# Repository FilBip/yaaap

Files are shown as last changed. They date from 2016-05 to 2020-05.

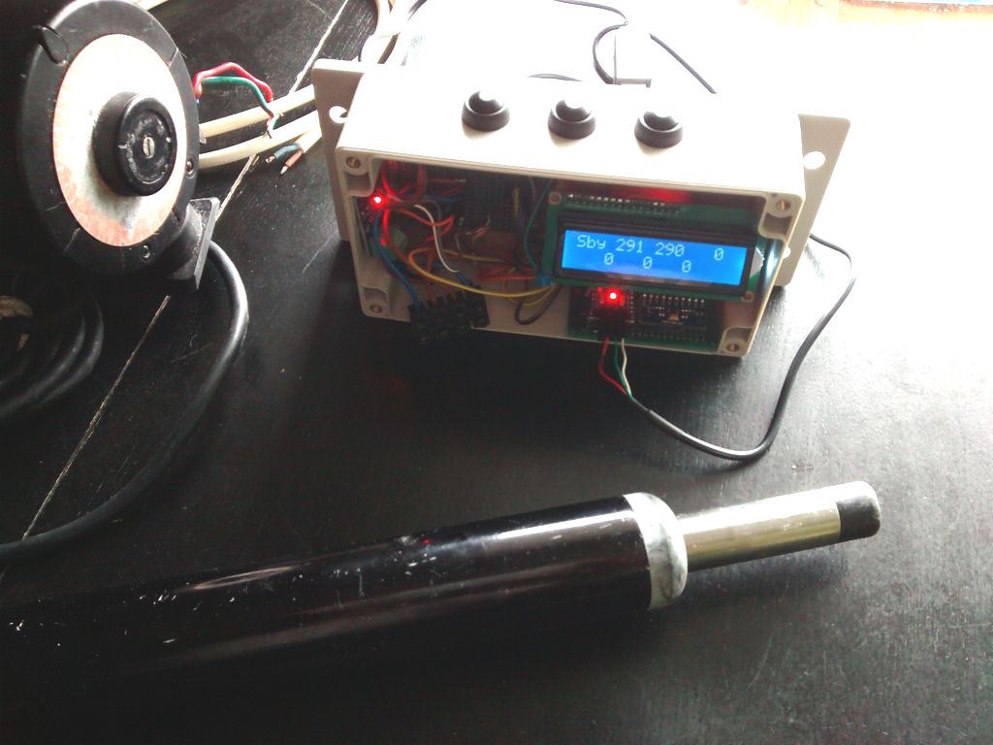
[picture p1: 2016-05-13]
yaaap-wip2.jpg

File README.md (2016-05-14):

# YAAAP Yet Another Arduino AutoPilot

Yaaap  is a simple autopilot for a sailboat using Arduino pro mini card and breakouts
The interface is reduced to 3 buttons and an LCD display.
The project was intended to replace the CPU of an old analog pilot Autohelm 2000 retaining the original electric actuator.

## Features

Heading is given by the 9dof IMU MPU9250 using the RTIMUlib for Arduino by Richards-Tech.
RTIMUlib filter is especially effective to keep a steady course when the heel angle varies.
I reduced the impact of magnetometer instability with a reduced SLERP value: fusion.setSlerpPower(0.001)
The tiller actuator is the old cylinder from the original Autohelm 2000 tillerPilot (with Omron motor 2332 12V)
Typical current for this motor is 1.6A. The cheap TB6612FNG can drive this motor with the 2 channels in parrallel (typical 2A to peak 6A).
It can be replaced by a more powerfull driver like IBT_2 with BTN7970B. 
I dropped the usage of PWM with my old small motor. Minimal pulse is 10ms, increasing to continuous depending on the computed command(PID).
There is no device to read the tiller position. Current to the motor is controlled to detect end of course or overload (ACS712).
The interface is minimal, made of 3 buttons using OneButtons library https://github.com/mathertel/OneButton
The LCD display is an I2C version.
   
## Instructions
The device is fixed behind the tiller facing the route.
Button 1 on the left: sarboard/less fonctions
button 2 on center: select/run-standby fonctions
Button 3 on the right: port/plus fonctions
	
### Startup
On startup, after initialization, the device is on standby, bearing to the current direction.
The display shows the status(Sby/Run), baering, heading and error (difference to baering).
   
### Run
click once on button 2.

### During run
click on button 1 or 3 increases (resp. decrease) 1 deg of bearing.
long press on button 1 or 3 increases (resp. decreases) 20 deg of bearing
long press on button 2 resets bearing to current heading
long press on button 1 and 2 (starboard and select) to tack to starboard
long press on button 3 and 2 (port and select) to tack to port
double click on button 2 to stop motor and standby
	
### During standby
long press button 1 push the tiller
long press button 3 pull the tiller
long press on button 2 resets bearing to current heading
long press button 1 and 3 to enter setup

### On setup first level
click 1(-) for dimmed backlight
click 3(+) for full backlight
click 2(sel) to enter setup menu
### On setup menu
click 1(-) to go to previous menu item
click 3(+) to go to next menu item
click 2(sel) to select menu item
### On setup item
click 1(-) to decrease value if applicable
click 3(+) to increase value if applicable
click 2(sel) to validate entry/value

### Calibration
To calibrate the compass, chose the menu item, draw 8 with the device. The display shows the offsets.
Click button 2 when OK.

### Configuration saving
Go to the saving menu item and validate to write calibration and other parameters to EEPROM

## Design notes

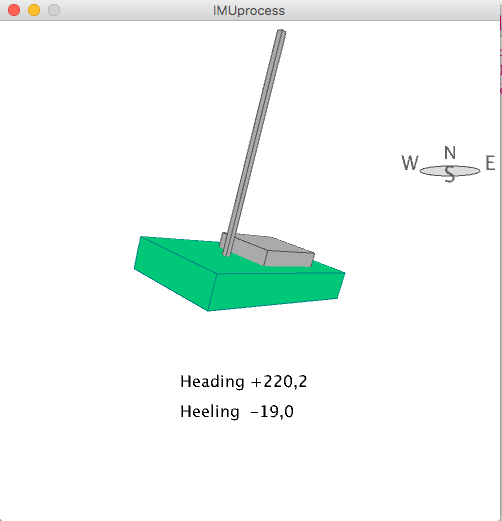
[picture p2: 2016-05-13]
YaaapProcessing/Processing snapshot.png

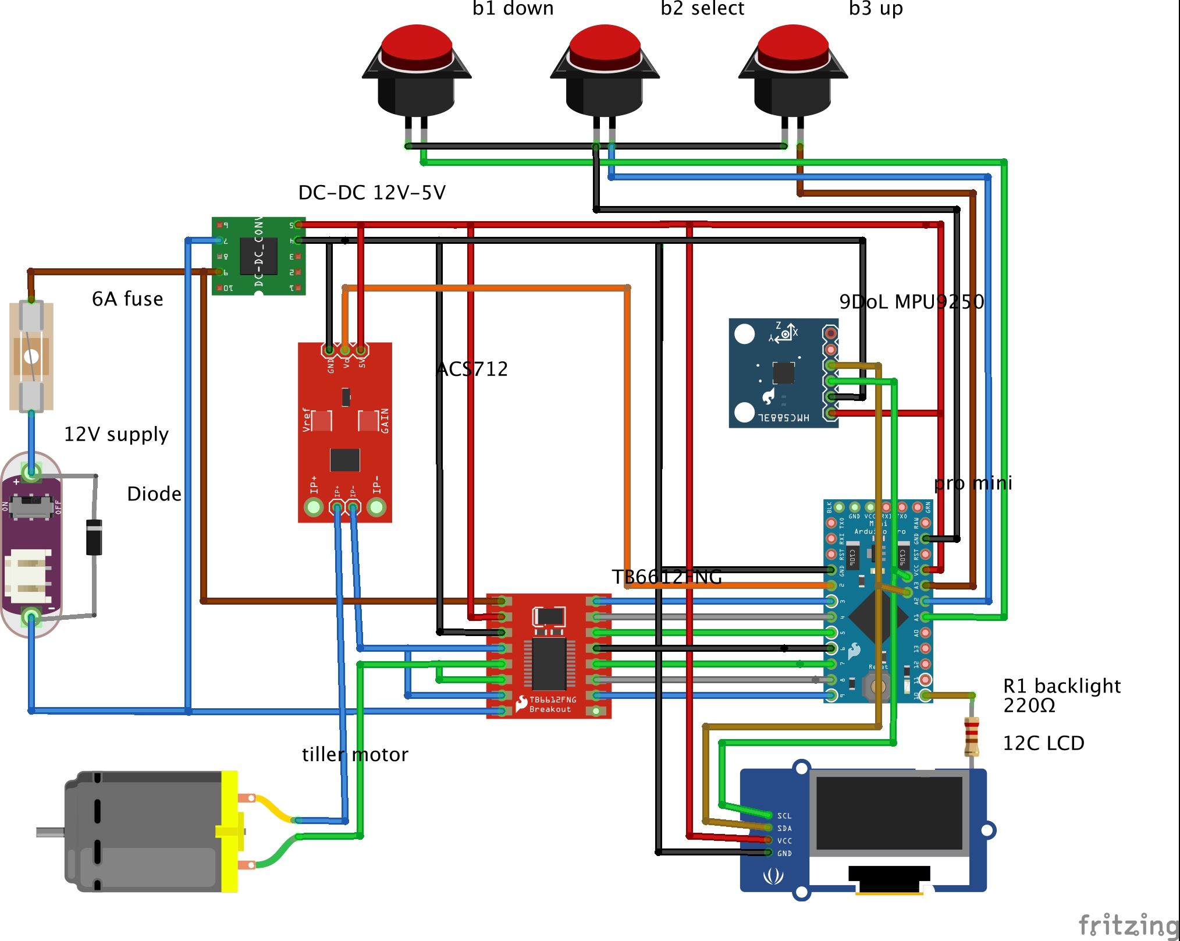
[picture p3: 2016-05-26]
fritz/yaaap_bb.jpg

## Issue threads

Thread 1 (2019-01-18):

yaaap.ino computeCmd function

odani, 2019-01-18:
Hi, can you confirm that line 363 in yaaap.ino is not necessary and that cmd should be computed on line 381 every time?

This is great code. I'm working on using it with a oled screen and a pololu lsm303 compass.

FilBip, 2019-01-18:
Hi,
on line 383, cmd should be computed... if not in deadband :)
A test "if (cmd != 0) cmd = ..." should be added on 383 or the bracket on 372 has to be moved after 383.

Code is not so great :))

regards

----- Mail original -----
De: "odani" <notifications@github.com>
À: "FilBip/yaaap" <yaaap@noreply.github.com>
Cc: "Subscribed" <subscribed@noreply.github.com>
Envoyé: Vendredi 18 Janvier 2019 02:21:40
Objet: [FilBip/yaaap] yaaap.ino computeCmd function (#1)

Hi, can you confirm that line 363 in yaaap.ino is not necessary and that cmd should be computed on line 381 every time?

This is great code. I'm working on using it with a oled screen and a pololu lsm303 compass.

—
You are receiving this because you are subscribed to this thread.
Reply to this email directly, view it on GitHub , or mute the thread .

FilBip, 2019-01-18:
My previous reply is wrong. The right solution is to move the bracket from 372 to 384.

----- Mail original -----
De: "odani" <notifications@github.com>
À: "FilBip/yaaap" <yaaap@noreply.github.com>
Cc: "Subscribed" <subscribed@noreply.github.com>
Envoyé: Vendredi 18 Janvier 2019 02:21:40
Objet: [FilBip/yaaap] yaaap.ino computeCmd function (#1)

Hi, can you confirm that line 363 in yaaap.ino is not necessary and that cmd should be computed on line 381 every time?

This is great code. I'm working on using it with a oled screen and a pololu lsm303 compass.

—
You are receiving this because you are subscribed to this thread.
Reply to this email directly, view it on GitHub , or mute the thread .

odani, 2019-01-18:
That makes sense. I’ll try it this weekend.

Also, do you have any suggestions for the Kd and Kp values? I see you have
3 and 30 in your code, but was wondering if you found that to be best, or
some other values to work better. I imagine it depends on the helm, sea
state and the actuator

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

FilBip, 2019-01-18:
Yes Kp and Kd depend on the actuator etc.
The code lacks an automatic correction depending on the sea. Not easy with 32KB of memory.
The next version will by a pypilot on raspberry :)

----- Mail original -----
De: "odani" <notifications@github.com>
À: "FilBip/yaaap" <yaaap@noreply.github.com>
Cc: "FilBip" <plq@free.fr>, "Comment" <comment@noreply.github.com>
Envoyé: Vendredi 18 Janvier 2019 14:51:51
Objet: Re: [FilBip/yaaap] yaaap.ino computeCmd function (#1)

That makes sense. I’ll try it this weekend.

Also, do you have any suggestions for the Kd and Kp values? I see you have
3 and 30 in your code, but was wondering if you found that to be best, or
some other values to work better. I imagine it depends on the helm, sea
state and the actuator

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

—
You are receiving this because you commented.
Reply to this email directly, view it on GitHub , or mute the thread .

odani, 2019-01-20:
I like how simple the arduino is. I took a look at the source code for
pypilot, and it's much more complicated.

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

odani, 2020-05-03:
In the main loop, you have
`int ctrl=0;`
but I think this needs to be placed outside the loop. Otherwise the computed ctrl is forgotten, and tillerCommand(ctrl) where ctrl=0 gets called with each loop where the ctrl is not computed. The result is that each pulse is very short (20ms), and I don't think that's the intention.

FilBip, 2020-05-03:
My pilot had been out of service for more than a year. With a burnt motor driver.
I woke him up after your remark. The behavior is more linear with this correction. The code is now modified on github.
Thank you odani 👍

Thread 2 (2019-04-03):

Motor only drives for a second

dailyroach, 2019-04-03:
Hi , I set everything up correctly "I think" but the LCD displays overload every time I try to move the tiller motor . The motor trys to drive but only for a split second any ideas why this would be happening ?

dailyroach, 2019-04-04:
Tried an IBT-2 motor controller but not sure what I needed to change in the code or wiring regardless I followed my nose but alas still not working .

odani, 2020-05-03:
Hi, I think you need to see how much current the motor is drawing (during normal operation and when it has been overloaded) by using the current sensor. Then you'd need to update the OVERLOADCURRENT parameter at the top of the code.

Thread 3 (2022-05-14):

It is possible to scoll after Item 6 of menu. Causes problem

whydee, 2022-05-14:
In setupmenu,
      case 'u':
        if (line < LINES) line++;

should be changed into
      case 'u':
        if (line < LINES-1) line++;

FilBip, 2022-05-14:
setupmenu source code modified. Thanks whydee ;)

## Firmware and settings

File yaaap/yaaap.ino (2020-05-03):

/*
   YAAAP Yet Another Arduino AutoPilot
   yaaap.ino
   2016 Philippe Leclercq

   Heading is given by the 9dof IMU MPU9250 using the RTIMUlib for Arduino by Richards-Tech.
   RTIMUlib filter is especially effective to keep a steady course when the heel angle varies.
   I reduced the impact of magnetometer instability with a reduced SLERP value: fusion.setSlerpPower(0.001)
   The tiller actuator is the old cylinder from the original Autohelm 2000 tillerPilot (with Omron motor 2332 12V)
   Typical current for this motor is 1.6A. The cheap TB6612FNG can drive this motor with the 2 channels in parrallel (2A typical to 6A peak).
   It can be replaced by a more powerfull driver like IBT_2 with BTN7970B.
   I dropped the usage of PWM with my old small motor. Minimal pulse is 10ms, increasing to continuous depending
   on the computed command(PID).
   There is no device to read the tiller position. Current to the motor is controlled to detect end of course or overload (ACS712).
   The interface is minimal, made of 3 buttons using OneButtons library https://github.com/mathertel/OneButton
   The LCD display is an I2C version.

   Instructions
	The device is fixed behind the tiller facing the route.
 	Button 1 on the left: sarboard/less fonctions
	button 2 on center: , select/run-standby fonctions
	Button 3 on the right: port/plus fonctions

	On startup, after initialization, the device is on standby, bearing to the current direction.
	The display shows the status(Sby/Run), bearing, heading and error (difference to baering).

	To run, click once on button 2.

	During run, click on button 1 or 3 increases (resp. decrease) 1 deg of bearing.
				long press on button 1 or 3 increases (resp. decreases) 20 deg of bearing
				long press on button 2 resets bearing to current heading
				long press on button 1 and 2 (starboard and select) to tack to starboard
				long press on button 3 and 2 (port and select) to tack to port
				double click on button 2 to stop motor and standby

	During standby,	long press button 1 push the tiller
				long press on button 2 resets bearing to current heading
				long press button 3 pull the tiller
				long press button 1 and 3 to enter setup

				On setup first level,	click 1(-) for dimmed backlight
							click 3(+) for full backlight
							click 2(sel) to enter setup menu
				On setup menu,		click 1(-) to go to previous menu item
							click 3(+) to go to next menu item
							click 2(sel) to select menu item
				On setup item,		click 1(-) to decrease value if applicable
						        click 3(+) to increase value if applicable
							click 2(sel) to validate entry/value

	To calibrate the compass, chose the menu item, draw 8 with the device. The display shows the offsets.
	Click button 2 when OK.
	Important: go to the saving menu item and validate to write calibration and other parameters to EEPROM.

   */

#define DEBUG 0
#define SERIALDEBUG 0
//#define SERVO 1
#define TACKANGLE 100 // In degrees
#define OVERLOADCURRENT 2400 // milliAmps
#define OVERLOADDELAY 5000 // millisec
// motor definitions
//#define MOTORDRIVER 1 // BTN7970B
#define MOTORDRIVER 2 // TB6612FNG

#if MOTORDRIVER == 1 // BTN7970B
#define RPWM 3
#define LPWM 4
//#define R_EN 5
//#define L_EN 6
#elif MOTORDRIVER == 2 // TB6612FNG // Two channels in parallel for a 2Amp motor
#define A_PWM 3
#define A_IN2 4
#define A_IN1 5
#define STBY 6
#define B_IN1 7
#define B_IN2 8
#define B_PWM 9
#endif
#define ACS712PIN A0
#define BACKLIGHTPIN 10

#include <LiquidCrystal_I2C.h>
#include <Wire.h>
#include "OneButton.h"
#include "I2Cdev.h"
#include "RTIMUSettings.h"
#include "RTIMU.h"
#include "RTFusionRTQF.h"
#include "CalLib.h"


#define LED_PIN 13
unsigned long ledStart = 0;

// Setup OneButtons on pins A1, A2, A3
OneButton button1(A1, true);
OneButton button2(A2, true);
OneButton button3(A3, true);

long refVoltage = 0;

float cmd = 0;
bool standby = true;
bool launchTack = false;
byte deadband = 4;
float heading = 0, bearing = 0, headingError = 0;
float previousError = 0, deltaError = 0;
//float deltaErrorDeriv = 0, previousDeltaError = 0;
//int prevLoop = 0;
unsigned long previousTime = 0, deltaTime;
bool setupFonctions = false;
char keyPressed = ' ';
unsigned long prevDisplay = 0, prevCommand = 0;
#define COMMAND_INTERVAL   200   // interval between tiller command calculations
#define DISPLAY_INTERVAL  1000   // interval between heading displays

CALLIB_DATA params;              // the calibration data and other EEPROM params

int Kp = 3, Kd = 30; // proportional, derivative1 coefficients (tiller position do the integral/sum term)

// LCD display interface pins
//LiquidCrystal lcd(12, 11, 10, 9, 8, 7);
LiquidCrystal_I2C lcd(0x27, 16, 2);
#ifdef SERVO // For development and code test only
#include <Servo.h>
Servo myservo;
int servoAngle = 90;
#endif

/***********************************************************
   Subroutines
 ***********************************************************
*/
int sign(int val) { // declare the missing sign() fn
  return (val > 0) - (val < 0);
}

void printJustified(int value) {
  char buffer[7];
  sprintf(buffer, "%4d", value);
  lcd.print(buffer);
}
float map360(float deg) {
  if (deg < 0) deg += 360;
  else if (deg > 360) deg -= 360;
  return deg;
}
void beep(bool on) { // No sound, only a flashing led
  if (on) {
    digitalWrite(LED_PIN, true);
    ledStart = millis();
  }
  else if ((millis() - ledStart) > 100 ) {
    ledStart = 0; // End of beeb/light. Reset delay
    //   digitalWrite(LED_PIN, false);
  }
}

/***********************************************************
   Tiller/motor management
***********************************************************

*/
byte pulseState = LOW;
unsigned long pulseCurrentMillis;
unsigned long pulseStartMillis;
int tillerCurrent = 0;
int overloadDirection = 0;
unsigned long overloadStart = 0;

void tillerStandby(boolean state) {
  if (state == true) { // stop mode
#if MOTORDRIVER == 1 // BTN7970B
    analogWrite(RPWM, LOW);
    analogWrite(LPWM, LOW);
//    digitalWrite(R_EN, LOW);
//    digitalWrite(L_EN, LOW);
#elif MOTORDRIVER == 2 // TB6612FNG // Two channels in parallel for a 2Amp motor
    digitalWrite(A_PWM, LOW);
    digitalWrite(B_PWM, LOW);
#endif
    pulseState = LOW;
    digitalWrite(LED_PIN, false);
  }
}

void tillerInit() {
  // Init over current protection device (ACS712PIN)
  //  Serial.print("estimating avg. quiscent voltage:");
  //read X samples to stabilize value
  static const int nbSamples = 200;
  for (int i = 0; i < nbSamples; i++) {
    refVoltage += analogRead(ACS712PIN);
    delay(1);//depends on sampling (on filter capacitor), can be 1/80000 (80kHz) max.
  }
  refVoltage /= nbSamples;
#if SERIALDEBUG == 1
  Serial.print(map(refVoltage, 0, 1023, 0, 5000)); Serial.println(" mV");
#endif
#if MOTORDRIVER == 1 // BTN7970B
  analogWrite(RPWM, LOW);
  analogWrite(LPWM, LOW);
//  digitalWrite(R_EN, LOW);
//  digitalWrite(L_EN, LOW);
#elif MOTORDRIVER == 2 // TB6612FNG // Two channels in parallel for a 2Amp motor
  pinMode(STBY, OUTPUT);
  pinMode(A_PWM, OUTPUT);
  pinMode(A_IN1, OUTPUT);
  pinMode(A_IN2, OUTPUT);
  pinMode(B_PWM, OUTPUT);
  pinMode(B_IN1, OUTPUT);
  pinMode(B_IN2, OUTPUT);
  digitalWrite(STBY, HIGH);
#endif
  pulseStartMillis = millis();

  tillerStandby(true);
}

bool tillerOverload(int commandDirection) {
  const int sensitivity = 185;//change this to 100 for ACS712PIN-20A or to 66 for ACS712PIN-30A
  bool overload = false;
  if (overloadStart) {
    if (overloadDirection == commandDirection) {       // If same direction than last detected overload
      if ((millis() - overloadStart) < OVERLOADDELAY )  // wait delay
        overload = true;
      else {
        overloadStart = 0; // End of pause. Reset delay
      }
      return overload;
    }
    else {
      overloadStart = 0; // Direction has changed. Reset delay
    }
  }
  int current = 0;
  //read some samples to stabilize value
  for (int i = 0; i < 10; i++) {
    current = current + analogRead(ACS712PIN);
    delay(1);
  }
  current /= 10;
  current -=  refVoltage;
  tillerCurrent = current * 5000000 / 1023 / sensitivity; // to mA
  if (abs(tillerCurrent) > OVERLOADCURRENT) {
    overload = true;
    overloadStart = millis();
    overloadDirection = commandDirection;
    tillerStandby(true);
    lcd.setCursor(0, 1);
    lcd.print(F(" OVERLOAD "));
    lcd.setCursor(11, 1);
    lcd.print(tillerCurrent);
  }
  else {
    overloadDirection = 0;
  }
  return overload;
}

void tillerPush() {
#if MOTORDRIVER == 1 // BTN7970B
  analogWrite(LPWM, HIGH);
  analogWrite(RPWM, LOW);
#elif MOTORDRIVER == 2 // TB6612FNG // Two channels in parallel for a 2Amp motor
  digitalWrite(A_IN1, LOW);
  digitalWrite(A_IN2, HIGH);
  digitalWrite(B_IN1, LOW);
  digitalWrite(B_IN2, HIGH);
#endif
#ifdef SERVO
  servoAngle += 1;
  if (servoAngle > 180) servoAngle = 180;
  myservo.write(servoAngle);
#endif
}

void tillerPull() {
#if MOTORDRIVER == 1 // BTN7970B
  analogWrite(LPWM, LOW);
  analogWrite(RPWM, HIGH);
#elif MOTORDRIVER == 2 // TB6612FNG // Two channels in parallel for a 2Amp motor
  digitalWrite(A_IN1, HIGH);
  digitalWrite(A_IN2, LOW);
  digitalWrite(B_IN1, HIGH);
  digitalWrite(B_IN2, LOW);
#endif
#ifdef SERVO
  servoAngle -= 1;
  if (servoAngle < 0) servoAngle = 0;
  myservo.write(servoAngle);
#endif
}

void tillerCommand(int tillerCmd) {

  // Current / motor overload / end of course control
  if (tillerOverload(sign(tillerCmd)))
    tillerCmd = 0;

#if DEBUG == 10
  lcd.setCursor(0, 1);
  lcd.print("motor        ");
  lcd.setCursor(6, 1);
  lcd.print(tillerCmd);
  lcd.print(" ");
#endif

  if (tillerCmd == 0) {
    tillerStandby(true);
    pulseStartMillis = millis();
    return;
  }

  pulseCurrentMillis = millis();
  int pulseWidth = 20 + abs(tillerCmd) * 18 / 10; // Higher command, longer pulse (20 to 200ms)
  if ((pulseCurrentMillis - pulseStartMillis) <= pulseWidth) {
    pulseState = HIGH;
    digitalWrite(LED_PIN, true);
  }
  else {
    if (abs(tillerCmd) < 100) { // 100 => continuous 
      tillerCmd = 0;
      pulseState = LOW;
      digitalWrite(LED_PIN, false);
      //     Serial.print("pulseW="); Serial.print(pulseWidth); Serial.print(" "); Serial.print(pulseCurrentMillis); Serial.print(" - "); Serial.print(pulseStartMillis); Serial.println(" ");
#if DEBUG == 3
  lcd.setCursor(0, 1);
  printJustified(tillerCmd);
  lcd.print(" ");
  printJustified(pulseState);
  //printJustified(pulseWidth);
  lcd.print(" ");
#endif
    }
    pulseStartMillis = millis();
  }

  if (tillerCmd > 0)
    tillerPull();
  else
    tillerPush();

#if MOTORDRIVER == 1 // BTN7970B
//  digitalWrite(R_EN, pulseState);
//  digitalWrite(L_EN, pulseState);
#elif MOTORDRIVER == 2 // TB6612FNG // Two channels in parallel for a 2Amp motor
  digitalWrite(A_PWM, pulseState);
  digitalWrite(B_PWM, pulseState);
#endif
}

/***********************************************************
   Compute tiller command
 ***********************************************************
*/
int computeCmd() {
  headingError = heading - bearing;
  if (abs(headingError) < deadband / 2) {
    headingError = 0;
    cmd = 0;
  }
  else {
    if (abs(headingError) > 180) {
      if (bearing > heading)
        headingError += 360;
      else
        headingError -= 360;
    }
   unsigned long now = millis();
  deltaTime = now - previousTime;
  previousTime = now;
  deltaError = headingError - previousError;
  previousError = headingError;
 // deltaErrorDeriv = deltaError - previousDeltaError;
  //previousDeltaError = deltaError;

  cmd = Kp * headingError + (Kd * deltaError) * 1000 / deltaTime; // by time in sec
  if (cmd > 100) cmd = 100;
  if (cmd < -100) cmd = -100;
 }
#if DEBUG == 2
  // lcd.clear();
  lcd.setCursor(0, 1);
  //printJustified((int)(Kp*headingError));
  printJustified((int)(Kp * headingError ));
  printJustified((int)(Kd * deltaError * 1000 / deltaTime));
  printJustified((int)cmd);
  lcd.print("  ");
#endif
#if SERIALDEBUG==2
  Serial.print(deltaTime);
  Serial.print(" ");
  Serial.print(heading);
  Serial.print(" ");
  Serial.print(headingError);
  Serial.print(" ");
  Serial.print(deltaError);
  Serial.print(" ");
  Serial.println(cmd);
#endif
  return (int)cmd;
}
/***********************************************************
   Buttons management
 ***********************************************************
*/
// This function will be called when the button1 was pressed 1 time
void b1Click() { // One degree to starboard
  bearing = map360(bearing + 1);
  beep(true);
}
void b1LongPress() { // During button pressed
  if (standby)  {
    // During Standby, if buttons 1 and 3 pressed, setup/calibration
    // else move tiller
    if (button3.isLongPressed())
      setupFonctions = true;
    else
      tillerCommand(-100);
  }
  else {
    beep(true);
    if (!launchTack && button2.isLongPressed()) { // Tack if two buttons pressed
      launchTack = true;
      bearing = map360(bearing + TACKANGLE);
    }
  }
}
void b1LongPressStop() { // Move to starboard
  if (!launchTack) bearing = map360(bearing + 20);
  if (standby) tillerStandby(true); // Stop the tiller at the end of press during standby
}
void b2Click() { // standby / Run
  beep(true);
  standby = !standby;
  tillerStandby(standby);
}
/* Dbl click replaced by simple click
 *  
 void b2DoubleClick() { // standby on
  if (!standby) beep(true);
  standby = true;
  tillerStandby(standby);
}
*/
void b2LongPressStop() { // reset steering or launch tack
  beep(true);
  if (launchTack)
    launchTack = false; // steering update already done
  else {
    lcd.clear();
    lcd.print("Reset steering");
    bearing = heading;
    //    delay (100);
  }
}
void b3Click() { // One degree to badboard
  beep(true);
  bearing = map360(bearing - 1);
}
void b3LongPress() { // During button pressed
  if (standby)  {
    // During Standby, if buttons 1 and 3 pressed, calibration
    // else move tiller
    if (button1.isLongPressed())
      setupFonctions = true;
    else
      tillerCommand(+100);
  }
  else {
    beep(true);
    if (!launchTack && button2.isLongPressed()) { // Tack if two buttons pressed
      launchTack = true;
      bearing = map360(bearing - TACKANGLE);
    }
  }
}

void b3LongPressStop() { // Move to badboard
  if (!launchTack) bearing = map360(bearing - 20);
  if (standby) tillerStandby(true); // Stop the tiller at the end of press during standby
}

void buttonsInit() {
  static const int clickTicks = 300, pressTicks = 800;
  // link the button 1 functions.
  button1.setClickTicks(clickTicks);
  button1.setPressTicks(pressTicks);
  button1.attachClick(b1Click);
  // button2.attachDoubleClick(b1DoubleClick);
  //button1.attachLongPressStart(b1LongPressStart);
  button1.attachLongPressStop(b1LongPressStop);
  button1.attachDuringLongPress(b1LongPress);

  // link the button 2 functions.
  button2.setClickTicks(clickTicks);
  button2.setPressTicks(pressTicks);
  button2.attachClick(b2Click);
//  button2.attachDoubleClick(b2DoubleClick);
  //button2.attachLongPressStart(b2LongPressStart);
  button2.attachLongPressStop(b2LongPressStop);
  //button2.attachDuringLongPress(b2LongPress);

  // link the button 3 functions.
  button3.setClickTicks(clickTicks);
  button3.setPressTicks(pressTicks);
  button3.attachClick(b3Click);
  // button3.attachDoubleClick(b3DoubleClick);
  //button3.attachLongPressStart(b3LongPressStart);
  button3.attachLongPressStop(b3LongPressStop);
  button3.attachDuringLongPress(b3LongPress);
}

void buttonsTick() {
  beep(false);
  button1.tick();
  button2.tick();
  button3.tick();
}

/***********************************************************
   Initial setup
 ***********************************************************
*/
void setup() {

  Wire.begin(); // join I2C bus (I2Cdev library doesn't do this automatically)
#if SERIALDEBUG
  Serial.begin(115200);
  Serial.println("Initializing...");
#endif
  pinMode(LED_PIN, OUTPUT);
  pinMode(BACKLIGHTPIN, OUTPUT);

  //  lcd.setBacklight(1);
  lcd.begin();
  lcd.setCursor(0, 0);
  lcd.print("Init ");
  calLibRead(0, &params);                           // pick up existing mag data (and other params) if there
  Kp = params.Kp;
  Kd = params.Kd;
  analogWrite(BACKLIGHTPIN, params.backlight);
  deadband = params.deadband;
  lcd.print("*");
  buttonsInit();
  lcd.print("*");
  tillerInit();
  lcd.print("*");
  compassInit();
  lcd.print("*");
  bearing = compassHeading();

}

/***********************************************************
   Main loop
 ***********************************************************
*/

  float headingSum = 0;
  int headingCnt = 0;
  int ctrl = 0;

void loop() {
  /*
     Main loop
   	read keypad/buttons
   	read heading
   	compute steering (PID controller)
   	steer
  */
  
  buttonsTick();
  if (setupFonctions) {
    tillerCommand(0); // Security...
    setupMenu();
    compassReset(); // Reinit fusion algo after any pause
    setupFonctions = false;
  }
  // Sum for heading average
  headingSum += compassHeading();
  headingCnt++;
 
  unsigned long now = millis();

 // Periodic calculation of the steering control (with heading average)
  if ((now - prevCommand) >= COMMAND_INTERVAL) {
    prevCommand = now;
    heading = headingSum/headingCnt;
#if DEBUG == 1
  lcd.setCursor(0, 1);
  lcd.print(headingCnt);
  lcd.print(" ");
#endif
	  headingSum = 0;
	  headingCnt = 0;
    ctrl = computeCmd();
#if DEBUG == 1
  lcd.setCursor(5, 1);
  lcd.print(" ");
  lcd.print(ctrl);
  lcd.print(" ");
#endif
  }

  // Control running tiller actuator
  if (!standby)
      tillerCommand(ctrl);
	
  // Periodic display refresh
  if ((now - prevDisplay) >= DISPLAY_INTERVAL) {
    prevDisplay = now;

    lcd.setCursor(0, 0);
    if (standby)
      lcd.print("Sby");
    else
      lcd.print("Run");

    printJustified((int)bearing);
    printJustified((int)heading);
    printJustified((int)headingError);
    lcd.setCursor(0, 1);
//    printJustified(tillerCurrent);
    lcd.print(F("               "));

    lcd.print("   ");
  }

}

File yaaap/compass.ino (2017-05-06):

/*
   YAAAP Yet Another Arduino AutoPilot
   compass.ino
   2016 Philippe Leclercq

   9dof IMU breakout : MPU9250

   Uses RTIMUlib library https://github.com/richards-tech/RTIMULib-Arduino
	4 lines modified in RTIMUlib/RTIMULibDefs.h :
	//#define MPU9150_68                      // MPU9150 at address 0x68
	#define MPU9250_68                      // MPU9250 at address 0x68
	//#define RTIMU_XNORTH_YEAST              0                   // this is the default identity matrix
	#define RTIMU_XNORTH_YWEST              4


 */


#define SERIALDEBUG 0
//#define SERIALDEBUG 3 // Value to send yaw/pitch/roll to Processing sketch on host
#include <Wire.h>
#include "I2Cdev.h"
#include "RTIMUSettings.h"
#include "RTIMU.h"
#include "RTFusionRTQF.h"
#include "CalLib.h"
#include <EEPROM.h>

RTIMU *imu;                                           // the IMU object
RTFusionRTQF fusion;                                  // the fusion object
RTIMUSettings settings;                               // the settings object
unsigned long lastDisplay;
unsigned long lastRate;
int sampleCount;
#define DISPLAY_POSE_INTERVAL  500                         // interval between pose displays

/***********************************************************
   Compass management
 ***********************************************************
*/
float compassHeading() {
  float yaw;
  //  int loopCount = 1;
#if SERIALDEBUG
  unsigned long now = millis();
  unsigned long delta;
#endif
  int loopCount = 1;

  while (imu->IMURead()) {                                // get the latest data if ready yet
    // this flushes remaining data in case we are falling behind
    if (++loopCount >= 10)           continue;
    fusion.newIMUData(imu->getGyro(), imu->getAccel(), imu->getCompass(), imu->getTimestamp());
#if SERIALDEBUG == 1

    sampleCount++;
    if ((delta = now - lastRate) >= 1000) {
      Serial.print("Sample rate: "); Serial.print(sampleCount);
      if (imu->IMUGyroBiasValid())
        Serial.println(", gyro bias valid");
      else
        Serial.println(", calculating gyro bias");

      sampleCount = 0;
      lastRate = now;
    }

    if ((now - lastDisplay) >= DISPLAY_POSE_INTERVAL) {
      lastDisplay = now;
      RTMath::display(" Gy", (RTVector3&)imu->getGyro());                // gyro data
      RTMath::display(" Ac", (RTVector3&)imu->getAccel());              // accel data
      RTMath::display(" Ma", (RTVector3&)imu->getCompass());              // compass data
      RTMath::displayRollPitchYaw(" Pos", (RTVector3&)fusion.getFusionPose()); // fused output
      Serial.println();
    }
#endif
  }
#if SERIALDEBUG == 3 // Sends to Processing view
  if ((now - lastDisplay) >= 20) {
    lastDisplay = now;
    if (imu->IMUGyroBiasValid()) {
      Serial.print(fusion.getFusionPose().z()); // yaw
      Serial.print(","); // print comma so values can be parsed
      Serial.print(fusion.getFusionPose().y()); // pitch
      Serial.print(","); // print comma so values can be parsed
      Serial.println(fusion.getFusionPose().x()); // roll
      //  delay(10);
    }
  }
#endif
  yaw = map360(fusion.getFusionPose().z() * RTMATH_RAD_TO_DEGREE);
  //  yaw = fusion.getFusionPose().z() * RTMATH_RAD_TO_DEGREE;
#if SERIALDEBUG==2
  Serial.print("yaw=");
  Serial.println(yaw);
#endif
  return yaw;
}

void compassReset() {
  int errcode = imu->IMUInit();
#if SERIALDEBUG==1
  if (errcode < 0) {
    Serial.print("Init IMU failed: "); Serial.println(errcode);
  }
#endif
}

void compassInit() {
  RTVector3 gyroBias;
#if SERIALDEBUG==1
  for (int i = 0; i < 3; i++) {
    Serial.print(params.magMin[i]); Serial.print(" "); Serial.println(params.magMax[i]);
  }
  Serial.print(params.Kp); Serial.print(" "); Serial.print(params.Kd); Serial.print(" "); Serial.println(params.Kdd);
#endif
  imu = RTIMU::createIMU(&settings);                        // create the imu object
#if SERIALDEBUG==1
  Serial.print("ArduinoIMU starting using device "); Serial.println(imu->IMUName());
#endif
  int errcode = imu->IMUInit();
#if SERIALDEBUG==1
  if (errcode < 0) {
    Serial.print("Init IMU failed: "); Serial.println(errcode);
  }
#endif

  if (params.gyroBiasValid == 0x1) { // load gyroBias data if found on EEPROM
    gyroBias.setX(params.gyroBias[0]);
    gyroBias.setY(params.gyroBias[1]);
    gyroBias.setZ(params.gyroBias[2]);
    imu->setGyroBias(gyroBias);
  }

  bool cal = imu->getCalibrationValid();
#if SERIALDEBUG==1
  if (cal)
    Serial.println("Using calibration");
  else
    Serial.println("No valid calibration data");
#endif

#if SERIALDEBUG==2
  lastDisplay = lastRate = millis();
  sampleCount = 0;
#endif

  // Slerp power controls the fusion and can be between 0 and 1
  // 0 means that only gyros are used, 1 means that only accels/compass are used
  // In-between gives the fusion mix.

  fusion.setSlerpPower(0.003);

  // use of sensors in the fusion algorithm can be controlled here
  // change any of these to false to disable that sensor

  fusion.setGyroEnable(true);
  fusion.setAccelEnable(true);
  fusion.setCompassEnable(true);

  int loopCount = 0;
  do {
    compassHeading();
  } while ( ! imu->IMUGyroBiasValid() || ++loopCount < 20); // at least a few loop for a good initial baering
}

void compassCalibration() {
#if SERIALDEBUG==3 // Only 32k or memory in pro mini's ATMega328 chip. No calibration if debug...
}
#else
  int tmpOffX = 0, tmpOffY = 0, tmpOffZ = 0;
  RTVector3 mag;


  // calLibRead(0, &params);                           // pick up existing mag data if there

  params.magValid = false;
  for (int i = 0; i < 3; i++) {
    params.magMin[i] = 10000000;                    // init mag cal data
    params.magMax[i] = -10000000;
  }

  imu->setCalibrationMode(true);                     // make sure we get raw data

  keyPressed = ' ';
  while (keyPressed == ' ') { // Waiting any key

    if (imu->IMURead()) {                                 // get the latest data
      mag = imu->getCompass();
      for (int i = 0; i < 3; i++) {
        if (mag.data(i) < params.magMin[i]) {
          params.magMin[i] = mag.data(i);
        }
        if (mag.data(i) > params.magMax[i]) {
          params.magMax[i] = mag.data(i);
        }
      }
    }

    // Calculate offsets
    tmpOffX = (params.magMax[0] + params.magMin[0]) / 2;
    tmpOffY = (params.magMax[1] + params.magMin[1]) / 2;
    tmpOffZ = (params.magMax[2] + params.magMin[2]) / 2;

    lcd.setCursor(0, 1);
    lcd.print(tmpOffX);
    lcd.print(" ");
    lcd.print(tmpOffY);
    lcd.print(" ");
    lcd.print(tmpOffZ);
    lcd.print(" ");
    delay(20);
    buttonsTick();
  }
  // Save data if select key pressed, else exit
  if (keyPressed == 's') {
    params.magValid = true;
    calLibWrite(0, &params);
    compassInit();
  }
  else {
    lcd.setCursor(0, 1);
    lcd.print(F("*** Aborted ***"));
  }
  delay(1000);
}
#endif

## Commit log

2016-05-13 initial version
    [yaaap.fzz]
2016-05-13 gyroBias data saved to EEPROM
    for a better giron bras init when moving during initialization
2016-05-21 Update 20160521
    PID update
    Display update
    Overcurrent update
2016-05-21 20160522 update
    deadband param added
    Frizzing modified
    [yaaap.fzz]
2016-05-26 fritzing update
    [yaaap.fzz]
2022-05-14 Update setupMenu.ino
    Issue #3 correction
    [setupMenu.ino]
